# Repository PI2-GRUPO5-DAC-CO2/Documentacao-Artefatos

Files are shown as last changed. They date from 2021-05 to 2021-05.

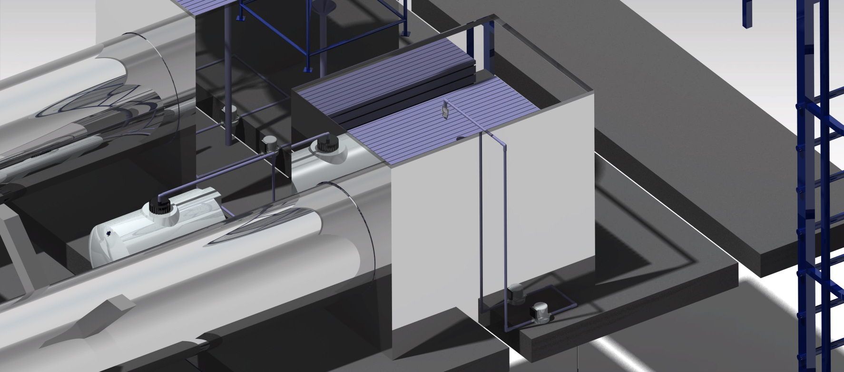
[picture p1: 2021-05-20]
Engenharias/Estruturas/PC3/Prints FINAIS/RENDER 4.jpg

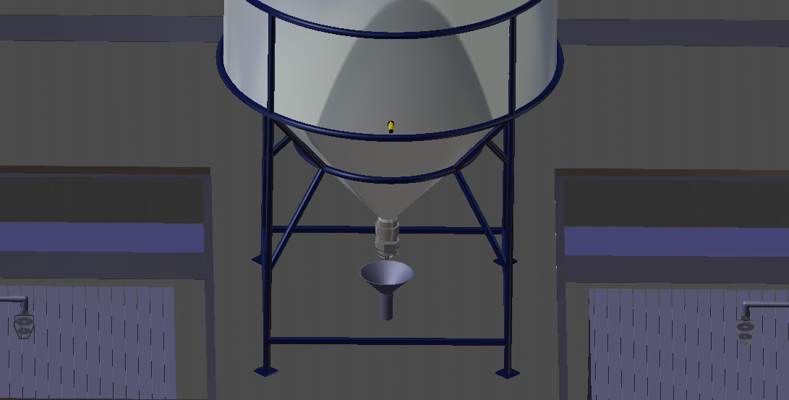
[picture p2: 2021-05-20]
Engenharias/Eletrônica/Integração/Integração - estrutura/Prints da Integração/Reservatorio Hidroxido.jpg

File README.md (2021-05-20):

# Projeto CATARCO

## Os links das apresentações  se encontram a seguir.

Ponto de controle 1: https://youtu.be/nJo-AYe7SZ8      

Ponto de controle 2: https://youtu.be/koXnGq-lNKc             

Ponto de controte 3: https://youtu.be/X2KLboLLJJk               

Feira de inovação de Tecnologia - FIT: https://youtu.be/X2KLboLLJJk

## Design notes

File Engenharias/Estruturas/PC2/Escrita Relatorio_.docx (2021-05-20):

Estrutura Externa

1 Materiais e justificativa

1.2Reservatórios

1- NA2CO3-- FEITO

2- CA(OH)2 -- Feito

3-NAOH --FEITO

4- CaCO3-- FEITO

1.6-Tubulações

Simulação estrutural

-NAOH---

-CAO3--

CA(OH2)- Geometria

Para a solução do formato do reservatório,foi levado em consideração o estado físico do CA(OH 2), por ser sólido em temperatura ambiente em forma de Pó fino, para transportá-lo para outros processos necessitaria a disposição de uma bomba especial. Por esse motivo, o reservatório foi instalado na parte superior da estrutura, usando a gravidade para o seu transporte. A geometria que mais se encaixa na solução é a cônica, onde não tem necessidade de intervenção para para descer. O volume calculado para o armazenamento do CACO3 é cerca de 756L, foi dimensionado um reservatório de capacidade 800L, para encontrar soluções prontas na indústria.

NA2CO3- - Geometria

Para o armazenamento da substância NA2CO3, foi calculada que o volume necessário é 192L, no entanto a disposição do tanque será na parte de cima da estrutura, onde não podemos ter um reservatório de alto pois impedia instalação por causa dos ventiladores, foi usado a solução de reservatório horizontal de capacidade de 230 Litros, onde os suportes são feito do mesmo material do reservatório, como mostrado na FigX

CACO3-DEFINIÇÃO GEOMETRIA

A Definição de geometria do reservatório, levou em consideração as soluções usadas comercialmente para armazenamento de substâncias químicas, pensando em ser em ter o maior volume com a menor área ocupada, foi escolhida novamente a forma Cilíndrica e fundo cônico ccmo na Fig X

CACO3-DEFINIÇÃO Suporte

O suporte foi dimensionado com o mesmo perfil tubular do NaOH, com 1 Polegada Com 1,5 mm de diâmetro interno, sendo todo o peso sustentado pelo tubo de raio menor junto com os suportes laterais, e os tubos superiores evitando o deslocamento do reservatório, deixando a estrutura mais estática possível .

CACO3-DEFINIÇÃO Material

O material utilizado nos suportes foi padrão para todos os os reservatórios, o aço 316,por possuir ótima propriedades mecânicas e possui uma ótima resistência à corrosão em comparação a outros tipos de aço.

CACO3-DEFINIÇÃO Qualidade da malha

Para a geração da malha, foi levada em consideração uma maior geração de elementos onde a estrutura vai ser sofrer mais esforços, nos suporte circulares,e nas pernas de apoio, foi utilizado uma malha de 5mm, onde encontramos uma qualidade satisfatória para realizar a simulação , Fig podemos ver que mesmo não.

CACO3-DEFINIÇÃO Condições de Contorno

São similares aos reservatório de NaOH e CaOH2, por se tratar de um sistema estático de armazenamento, únicos esforços são a força peso feita massa de Cao3 no sistema, com o valor máximo de 330 KG com o peso do suporte, foi considerado uma carga de 3300N como na Fig X

CACO3-DEFINIÇÃO Análise estática e resultados

A partir das condições de contorno aplicadas à geometria, a análise estática do suporte foi feita sob o modelo de flexão, o critério adotado em outros tópicos é de tensão de escoamento do material Tab X. Com a análise visa o resultados tensão de von Mises e o valor de deformação total do material que seguem descritos nas Fig. X e X

Os resultados obtido mostram que a estrutura atende muito bem a solicitações exigidas para o que foi projetada, com o deslocamento máximo de 0.061 mm e tensão de 20.417 MPA, sendo menor que a tensão de escoamento do material de 250 MPA,

NAOH-DEFINIÇÃO GEOMETRIA

Para o reservatório de naoh foi calculado o volume de 121 L para o sistema pode fazer um ciclo processamento do Co2, e levando em consideração que a norma NBR-15762 pede um volume de sgurança 30 \%, foi dimensionado um volume total de 160 L, utilizando a forma cilíndrica que o padrão reservatórios de PEAD.

NAOH-Definição suporte e geometria

Para a estrutura de suporte do reservatório, foi escolhido o modelo já utilizado comumente utilizado pela indústria, suporte tubular de 1 Polegada e 1,5 mm de diâmetro. O suporte como visto na fig X, concentra todo peso no anel tubular de menor raio, junto com suportes laterais, o mesmo foi projetado para receber somente carga do peso do reservatório mais fator de segurança.

Definição do material}

O material utilizado na estrutura foi o Aço 316, por causa das suas ótima propriedades químicas e mecânicas já comentadas no tópicos X

Qualidade da malha}

Para geração da malha, foi considerado onde a estrutura tem mais esforços, o suporte anelar do meio sustenta toda a estrutura, juntos com suportes laterais, então a malha foi maior refinada na área a ter encontrar um valor de qualidade aceitável para validação da solução, como mostra a FIG X

Condições de contorno}

Por se tratar de um reservatório estático onde não temos nenhuma força além da massa armazenada, foi utilizado a carga de 2700 N sobre as faces do suporte circular para validar o uso com seu volume máximo de 160 L , aproximadamente 258 KG de Naoh .

Análise estática e resultados}

Analisando o resultado dos esforços da gerados na geometria , a análise estática da estrutura foi feita considerando o modelo de flexão, a deformação máxima do suporte foi de 0.59 mm no anel de suporte como mostrado na Fig X, a tensão de von Mises máxima calculada de 110,13 MPA, mostrado na Fig X, sendo bem menor que 250 MPA de tensão de escoamento do material. Dessa forma temos 2.27 de fator de segurança

1- NA2CO3

- Para armazenar a solução de NA2CO3, figura X não se encontra dificuldade para a seleção de material para armazenar , já que a solução não é corrosiva e não reage facilmente com qualquer substância conforme a FISPQ e conforme a ABNT NBR 14725-2:2019 essa mistura não se encaixa em produto não corrosivo, ou seja não há exigências específicas da legislação para armazenamento e transporte , somente o cuidado para manter na temperatura adequada, e em ambiente fechado.
- Como não temos limitação de material a ser armazenado, vamos utilizar uma solução bem conhecida da indústria, o Polietileno,. Material leve e de natureza não polar, ele possui alta estabilidade agentes químicos e outros meios, sendo resistentes a soluções aquosas de sais, ácidos inorgânicos e álcalis(FISPQ). Até 74 graus, os PE são estáveis a muitos solventes. Como vamos trabalhar com NaoH em algumas partes do processo do CARTAGO, é importante assegurar que, caso o reservatório de carbonato de sódio tenha contato com a solução, o mesmo não seja afetado quimicamente.
- o PE tem propriedades mecânicas e térmicas que satisfazem os requisitos definidos no PC1, como mostra a Tabela X

| Normas | PEAD
Tensão de escoamento (Mpa) | D-637 | 26
Temperatura mínima e máxima em uso contínuo | | - 40 / + 90°C
Temperatura de Deflexão Térmica ( Celsus) | D-648 | 74
Resistência a Bases fortes | ASTM D543 | Resistente
Alongamento até a ruptura (%) | DIN 53452 / ASTM D638 / ISO R 527 | 500%
Tensão de escoamento à tração (MPA) | DIN 53455 / ASTM D638 / ISO R 527 | 29 MPa

Tabela: Propriedades mecânica e Térmicas PP

Referência :

FISPQ

http://csmpq.com.br/wp-content/uploads/2017/11/FISPQ-11-Carbonato-de-S%C3%B3dio-07_2015.pdf

1- CA(OH)2

A substância CA(OH)2, também conhecida como Cal hidratada, é um produto químico muito utilizado na indústria de cimentos, de tratamento de água e na indústria civil na composição de tintas, argamassas e gessos. (FIGUEROA). Sólido em temperatura ambiente, é armazenado em forma de PÓ conforme a ABNT NBR 10790- 2016, é classificado como tóxico pela norma ABNT NBR 14725-4, no entanto não é classificado como perigoso e as normas não especificam material para armazenamento, somente cuidado de movimentação, pois é tóxico e precisa de EPIs específicos para uso.

Para a definição dos materiais do reservatório, Imagem X, levamos em conta, a absorção do material a água, já que a cal reage água de forma exotérmica ,peso específico ,resistência química para o NaOH, capacidade de armazenamento de substâncias sólidas e facilidade de soluções prontas na indústria. A tabela X de matriz de decisão foi feita para melhor visualização dos pesos.O PEAD foi o material escolhido por ter a maior nota, e por isso se adequa a nossa solução.

Matriz de decisão do material
Critérios | Peso | PEAD | Aço Inox 316 | Fibra de Vidro
Massa específica | 7 | 8 | 6 | 8
Preço | 8 | 8 | 5 | 6
Resistência mecânica | 6 | 8 | 9 | 8
Resistência à Corrosão | 9 | 9 | 9 | 9
Resultado | | 186 | 154 | 170

\begin{table}[]

\begin{tabular}{|c|c|c|c|c|}

\hline

\multicolumn{5}{|c|}{Matriz de decisão do material} \\ \hline

Critérios & Peso & PEAD & Aço Inox 316 & Fibra de Vidro \\ \hline

Massa específica & 7 & 8 & 6 & 8 \\ \hline

Preço & 8 & 8 & 5 & 6 \\ \hline

Resistência mecânica & 6 & 8 & 9 & 8 \\ \hline

Resistência à Corrosão & 9 & 9 & 9 & 9 \\ \hline

Resultado & \multicolumn{1}{l|}{} & 186 & 154 & 170 \\ \hline

\end{tabular}

\end{table}

Referência:

FIGUEROA, Oscar O. Loli; NEPTUNE, André M. Louis. Influência da aplicação parcelada do Ca(OH)2 e do fósforo na produção de matéria seca do sorgo (Sorghum bicolor L. Moench) e nas principais formas de fósforo do solo. An. Esc. Super. Agric. Luiz de Queiroz, Piracicaba , v. 44, n. 2, p. 959-999, 1987 . Available from <http://www.scielo.br/scielo.php?script=sci_arttext&pid=S0071-12761987000200005&lng=en&nrm=iso>. access on 11 Apr. 2021. http://dx.doi.org/10.1590/S0071-12761987000200005.

ABNT NBR 10790- 2016

https://www.abntcatalogo.com.br/norma.aspx?ID=364269

ABNT NBR 14725-4

https://www.abntcatalogo.com.br/norma.aspx?ID=325473

1 . Reservatório de NAOH

- Para o reservatório de NAOH na Figura X foi encontrada uma série de restrições físicas e químicas e de normas impostas pela ABNT, ele é classificado pela norma ABNT 14725-4 como material altamente corrosivo e tóxico. A soda cáustica aquosa é uma substância muito corrosiva a materiais metálicos , como Alumínio, zinco, estanho e suas ligas, conforme a FISPQ do material. Recomenda-se a usar no reservatório materiais não reativos a NAOH, como aço carbono e aço inoxidável e certos compostos termoplásticos, como PP (Polipropileno) e PVC. Para a escolha do material levamos em consideração a temperatura de trabalho e de armazenamento do NAOH, pois em alta temperatura ele ataca o aço em altas temperaturas de trabalho. Outro fator importante a destacar é o biológico, a mistura ataca qualquer substância orgânica, e por isso é prejudicial ao homem, por isso no manuseio de substâncias deve levar em consideração a ABNT 16310. Como requisito de projeto, definido no Ponto de controle 1, o NAOh vai ser armazenado a uma temperatura máxima de 45 graus.
- Levando em consideração a FISPQ E ABNT 16310, os reservatórios que forem utilizar aço carbono ou aço inoxidável, é recomendado a não passar de 60 Graus, acima disso a aço precisa de tratamento diferente e adicionamento de substâncias, o que deixa o preço maior. Para o uso de termoplásticos, como a temperatura de uso recomendado pelas fabricantes é de 65 graus, variando com o nível de concentração.
- Levando em conta as informações e requisitos do sistema, a matriz de decisão X, traz informações dos principais materiais para essa aplicação, utilizando pesos que podem ser traduzidos em nível de importância para o projeto.Para a definição dos pesos, foi levado em consideração as necessidades do produto, facilidade de aquisição do material , modos e facilidades de fabricação e o custo de aquisição do material e do produto final. Estes pontos são destacados devido à natureza do projeto: um produto muito caro prejudica a instalação de diversas estações ao longo do terreno e o custo de material,a disponibilidade no mercado e as possibilidades de fabricação são fundamentais para o custo do produto.
- Conforme o resultado da matriz de decisão X, o PEAD é a melhor escolha para o projeto Cartaco, face aos materiais analisados. O Polipropeno é um material de fácil aquisição no mercado em diversas especificações,fácil logística, médio/baixo custo e pode ser encontrado com uma grande facilidade. Além disso, existem estudos técnicos, o que implica no maior conhecimento de suas propriedades e respostas devido ao seu manuseio e operação.
- \begin{table}[]
- \begin{tabular}{|c|c|c|c|c|c|}
- \hline
- \multicolumn{6}{|c|}{\textbf{Matriz de decisão do material}} \\ \hline
- Critérios & Peso & Polipropileno(PEAD) & Aço Inox 316 & Aço Duplex & Fibra de Vidro \\ \hline
- Massa específica & 4 & 8 & 6 & 8 & 8 \\ \hline
- Preço & 8 & 8 & 5 & 4 & 6 \\ \hline
- Resistência mecânica & 6 & 8 & 9 & 10 & 8 \\ \hline
- Resistência à Corrosão & 10 & 9 & 9 & 9 & 9 \\ \hline
- Resultado & \multicolumn{1}{l|}{} & \textbf{163} & 137 & 143 & 147 \\ \hline
- \end{tabular}
- \end{table}

Matriz de decisão do material
Critérios | Peso | Polipropileno(PEAD) | Aço Inox 316 | Aço Duplex | Fibra de Vidro
Massa específica | 4 | 8 | 6 | 8 | 8
Preço | 8 | 8 | 5 | 4 | 6
Resistência mecânica | 6 | 8 | 9 | 10 | 8
Resistência à Corrosão | 10 | 9 | 9 | 9 | 9
Resultado | | 163 | 137 | 143 | 147

PROPRIEDADES FÍSICAS | NORMAS | VALORES
Peso específico | DIN 53479 / ASTM D792 / ISO 1183 | 0,95 g/cm³
Temperatura mínima e máxima em uso contínuo | | - 40 / + 90°C
Tensão de escoamento à tração | DIN 53455 / ASTM D638 / ISO R 527 | 29 MPa
Resistência à bases fortes | ASTM D543 | resistente

Tabela PEAD

\begin{table}[]

\begin{tabular}{llllll}

\cline{1-3}

\multicolumn{1}{|l|}{PROPRIEDADES FÍSICAS} & \multicolumn{1}{l|}{NORMAS} & \multicolumn{1}{l|}{VALORES} & & & \\ \cline{1-3}

\multicolumn{1}{|l|}{Peso específico} & \multicolumn{1}{l|}{DIN 53479 / ASTM D792 / ISO 1183} & \multicolumn{1}{l|}{0,95 g/cm³} & & & \\ \cline{1-3}

\multicolumn{1}{|l|}{Temperatura mínima e máxima em uso contínuo} & \multicolumn{1}{l|}{} & \multicolumn{1}{l|}{- 40 / + 90°C} & & & \\ \cline{1-3}

\multicolumn{1}{|l|}{Tensão de escoamento à tração} & \multicolumn{1}{l|}{DIN 53455 / ASTM D638 / ISO R 527} & \multicolumn{1}{l|}{29 MPa} & & & \\ \cline{1-3}

\multicolumn{1}{|l|}{Resistência à bases fortes} & \multicolumn{1}{l|}{ASTM D543} & \multicolumn{1}{l|}{resistente} & & & \\ \cline{1-3}

& & & & & \\

& & & & & \\

& & & & &

\end{tabular}

\end{table}

Referências :

FISQ

https://www.santos.sp.gov.br/static/files_www/conteudo/DadosAbertos/FISPQ%20Soda%20c%C3%A1ustica.pdf

ABNT

https://www.normas.com.br/visualizar/abnt-nbr-nm/34421/abnt-nbr16310-expedicao-transporte-rodoviario-e-recebimento-de-hidroxido-de-sodio-soda-caustica-em-solucao-a-g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

https://www.abntcatalogo.com.br/norma.aspx?ID=325473

1.3 Reservatório de CACO3

O carbonato de Cálcio, conforme a norma ABNT NBR 14725-2:2019, quanto a classificação, a solução é classificada como uma mistura na reativa e não corrosiva, a escolha do material não precisa ter os mesmo nível de rigidez que o reservatório de NAOH (Tópico) tem, pois a legislação não especifica materiais específicos para armazenamento. Levando isso em consideração, podemos simplificar a busca por materiais leves, baratos e de fácil manutenção e que seja inerte a solução de soda cáustica, caso tenha contato.

Nesse perfil temos o Polietileno PP, mesmo material utilizado no reservatório de Carbonato de sódio, resistente ao NaOh e tem ótima propriedades mecânicas, vista na tabela X INCOMPLAST.

O PP, é um material de fácil aquisição no mercado em diversas especificações, fácil logística e baixo custo, e para o reservatório de CaCo3 precisamos de um tanque como na figura X de capacidade menor que nos outros processos do Cartago.

| Normas | PEAD
Tensão de escoamento (Mpa) | D-637 | 26
Temperatura mínima e máxima em uso contínuo | | - 40 / + 90°C
Temperatura de Deflexão Térmica ( Celsus) | D-648 | 74
Resistência a Bases fortes | ASTM D543 | Resistente
Alongamento até a ruptura (%) | DIN 53452 / ASTM D638 / ISO R 527 | 500%
Tensão de escoamento à tração (MPA) | DIN 53455 / ASTM D638 / ISO R 527 | 29 MPa

Tabela: Propriedades mecânica e Térmicas PP

\begin{table}[]

\begin{tabular}{llllll}

\cline{1-3}

\multicolumn{1}{|l|}{} & \multicolumn{1}{l|}{Normas} & \multicolumn{1}{l|}{PEAD} & & & \\ \cline{1-3}

\multicolumn{1}{|l|}{Tensão de escoamento (Mpa)} & \multicolumn{1}{l|}{D-637} & \multicolumn{1}{l|}{26} & & & \\ \cline{1-3}

\multicolumn{1}{|l|}{Temperatura mínima e máxima em uso contínuo} & \multicolumn{1}{l|}{} & \multicolumn{1}{l|}{- 40 / + 90°C} & & & \\ \cline{1-3}

\multicolumn{1}{|l|}{Temperatura de Deflexão Térmica ( Celsus)} & \multicolumn{1}{l|}{D-648} & \multicolumn{1}{l|}{74} & & & \\ \cline{1-3}

\multicolumn{1}{|l|}{Resistência a Bases fortes} & \multicolumn{1}{l|}{ASTM D543} & \multicolumn{1}{l|}{Resistente} & & & \\ \cline{1-3}

\multicolumn{1}{|l|}{Alongamento até a ruptura (\%)} & \multicolumn{1}{l|}{DIN 53452 / ASTM D638 / ISO R 527} & \multicolumn{1}{l|}{500\%} & & & \\ \cline{1-3}

\multicolumn{1}{|l|}{Tensão de escoamento à tração (MPA)} & \multicolumn{1}{l|}{DIN 53455 / ASTM D638 / ISO R 527} & \multicolumn{1}{l|}{29 MPa} & & & \\ \cline{1-3}

& & & & &

\end{tabular}

\end{table}

Referências

INCOMPLAST. POLIPROPILENO (PP). 2019. Disponível em: <https://incomplast.

com.br/polipropilenopp/>. Acesso em: 1 abr. 2021.

2 -Tubulações

Para a escolha de materiais das tubulações, temos que levar em consideração que algumas partes do projeto vão ter contato com NaOH, outras não.

Para padronizar o projeto foi escolhido escolher somente um tipo de material para as tubulações.

Temos que escolher um material de uma longa vida útil, resistente ao trabalho com temperatura acima de 45 graus, e ação do NAOH, baixo custo, fácil manutenção e usinagem .

Foi elaborada uma matriz de decisão X para escolha do material dos tubos, a tabela traz informações dos principais materiais que é utilizado para essa aplicação e o resultado mais adequado para o projeto, utilizando pesos que podem ser traduzidos em nível de prioridade.

Com o CPVC (Cloriploreto de Vinila Clorado) como resultado da matriz de decisão, podemos dizer que é a melhor escolha para o projeto, por ser um material de fácil instalação e manutenção, boa resistência mecânica ,confiável para transportes de produtos químicos a altas temperaturas, até 90 graus. Além de ser um produto de fácil aquisição no mercado.

Matriz de decisão do material
Critérios | Peso | Polietileno | PVC | CPVC | Aço Inox
Incrustação/Perda de pressão | 7 | 8 | 7 | 8 | 7
Preço | 8 | 7 | 9 | 8 | 5
Resistência mecânica/Impactos/Pressão | 6 | 7 | 6 | 7 | 9
Resistência à Corrosão/Temperatura | 9 | 8 | 7 | 8 | 9
Massa específica | 7 | 9 | 8 | 8 | 5
Resultado | | 234 | 229 | 235 | 196

\begin{table}[]

\begin{tabular}{|c|c|c|c|c|c|}

\hline

\multicolumn{6}{|c|}{Matriz de decisão do material} \\ \hline

Critérios & Peso & Polietileno & PVC & CPVC & Aço Inox \\ \hline

Incrustação/Perda de pressão & 7 & 8 & 7 & 8 & 7 \\ \hline

Preço & 8 & 7 & 9 & 8 & 5 \\ \hline

Resistência mecânica/Impactos/Pressão & 6 & 7 & 6 & 7 & 9 \\ \hline

Resistência à Corrosão/Temperatura & 9 & 8 & 7 & 8 & 9 \\ \hline

Massa específica & 7 & 9 & 8 & 8 & 5 \\ \hline

Resultado & \multicolumn{1}{l|}{} & 234 & 229 & \textbf{235} & 196 \\ \hline

\end{tabular}

\end{table}

\begin{table}[]

\begin{tabular}{|l|l|l|}

\hline

PROPRIEDADES FÍSICAS & NORMAS & VALORES \\ \hline

Peso específico & DIN 53479 / ASTM D792 / ISO 1183 & 0,95 g/cm³ \\ \hline

Temperatura mínima e máxima em uso contínuo & & - 40 / + 90°C \\ \hline

Tensão de escoamento à tração & DIN 53455 / ASTM D638 / ISO R 527 & 29 MPa \\ \hline

Resistência à bases fortes & ASTM D543 & resistente \\ \hline

\end{tabular}

\end{table}

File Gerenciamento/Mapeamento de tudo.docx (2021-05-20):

Contator:

- Exaustor
  - Pás
  - Motor
  - Sensores
  - Atuador
    - automatizado
    - manual
  - Características
    - Vazão
    - potência
    - Dimensões …
- Estrutura de sustentação
- Quantidade
- Tempo da etapa
- Gasto energético
- Valor Total
- Simulações
- Filtro
  - Estrutura
    - material
    - Formato
      - Circular ou quadrado
      - colméia ou placas verticais por exemplo
    - Espessura
  - Sistema de recirculação do NaOH
    - bomba
    - tubulação
    - calha intermediária
    - atuadores
  - Quantidade
  - Sensores
  - Atuador
    - automatizado
    - manual
- Estrutura de sustentação
- Tempo da etapa
- Gasto energético
- Valor Total
- Simulações

Conexão 1 [Contator -> Reservatório 1]

- Tubulação
  - espessura da parede
  - material
  - Válvulas
  - Atuadores
    - manuais
    - automatizados
  - Sensores
  - Estrutura de sustentação
  - Tempo da etapa
  - Gasto energético
  - Valor Total
  - Simulações
- Bomba
  - tipo
  - sensores
  - atuadores
    - manuais
    - automatizados
- Estrutura de sustentação
- Tempo da etapa
- Gasto energético
- Valor Total
- Simulações

Reservatório 1 (NaCO3)

- Sensores
- atuadores
  - manuais
  - automatizados
- válvulas
- características
  - formato
  - dimensões
  - espessura da parede
  - peso
- Estrutura de sustentação
- Tempo da etapa
- Gasto energético
- Valor Total
- Simulações

Conexão 2 [Reservatório 1 -> Reator]

- Tubulação
  - espessura da parede
  - material
  - Válvulas
  - Atuadores
    - manuais
    - automatizados
  - Sensores
  - Estrutura de sustentação
  - Tempo da etapa
  - Gasto energético
  - Valor Total
  - Simulações

Reservatório 2 [Ca(OH)2]

- Sensores
- atuadores
  - manuais
  - automatizados
- válvulas
- características
  - formato
  - dimensões
  - espessura da parede
  - peso
- Estrutura de sustentação
- Tempo da etapa
- Gasto energético
- Valor Total
- Simulações

Conexão 3 [Reservatório 2 -> Reator]

- Tubulação
  - espessura da parede
  - material
  - Válvulas
  - Atuadores
    - manuais
    - automatizados
  - Sensores
  - Estrutura de sustentação
  - Tempo da etapa
  - Gasto energético
  - Valor Total
  - Simulações

Reator:

- Motor
- Pás
- Válvulas
- sensores
- Atuadores
  - manuais
  - automatizados
- Característica
  - material
  - Dimensões
  - Volume
  - formato
  - espessura da parede
- Estrutura de sustentação
- Tempo da etapa
- Gasto energético
- Valor Total
- Simulações

Conexão 4 [Reator -> Centrífuga]

- Tubulação
  - espessura da parede
  - material
  - Válvulas
  - Atuadores
    - manuais
    - automatizados
  - Sensores
  - Estrutura de sustentação
  - Tempo da etapa
  - Gasto energético
  - Valor Total
  - Simulações
- Bomba
  - tipo
  - sensores
  - atuadores
    - manuais
    - automatizados
- Estrutura de sustentação
- Tempo da etapa
- Gasto energético
- Valor Total
- Simulações

Centrífuga

- Válvulas
- tipo
- sensores
- atuadores
  - manuais
  - automatizados
- Estrutura de sustentação
- Tempo da etapa
- Gasto energético
- Valor Total
- Simulações

Conexão 5 [Centrífuga -> Reservatório 3]

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

Reservatório 3 [NaOH]

- Sensores
- atuadores
  - manuais
  - automatizados
- válvulas
- características
  - formato
  - dimensões
  - espessura da parede
  - peso
- Estrutura de sustentação
- Tempo da etapa
- Gasto energético
- Valor Total
- Simulações
- Estrutura de suporte

Conexão 6 [Reservatório 3 -> Contator]

- Tubulação
  - espessura da parede
  - material
  - Válvulas
  - Atuadores
    - manuais
    - automatizados
  - Sensores
  - Estrutura de sustentação
  - Tempo da etapa
  - Gasto energético
  - Valor Total
  - Simulações
- Bomba
  - tipo
  - sensores
  - atuadores
    - manuais
    - automatizados
- Estrutura de sustentação
- Tempo da etapa
- Gasto energético
- Valor Total
- Simulações

Conexão 7 [Centrífuga -> Reservatório 4]

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

Reservatório 4 [CaCO3]

- Sensores
- atuadores
  - manuais
  - automatizados
- válvulas
- características
  - formato
  - dimensões
  - espessura da parede
  - peso
- Estrutura de sustentação
- Tempo da etapa
- Gasto energético
- Valor Total
- Simulações
- Estrutura de suporte

Sala de operação

- Características
  - dimensões
- Sistema de contenção
- Disposição dos componentes
- Estrutura Externa
- Gasto energético
- Valor Total
- Simulações
  - Estrutura externa
- Central de Comando
  - Monitor
  - Painel

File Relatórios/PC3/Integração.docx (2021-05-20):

Integração

- Sistema de comunicação
  - João
  - (alguém de soft)
- Funções de software
- Relação das necessidades de eletrônica com as escolhas de energia
  - Marcelo
- Bombas, tubulações (Sugestão de nome para o tópico: Sistema de circulação para fluidos e sólidos)

- Marcelo

- Explicar porque tal sensor e atuador está localizado em tal lugar (Sugestão de nome para o tópico: Instalação de sistema eletrônico)
  - (Sugestão de nome para o tópico: Sistema de circulação para fluidos e sólidos)

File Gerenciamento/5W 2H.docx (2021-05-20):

Descrição do projeto

Para descrever o projeto CATARCO, foi utilizado a ferramenta 5W2H, termo que corresponde às iniciais (em inglês) de sete questionamentos capazes de guiar e sanar as principais dúvidas que podem surgir ao longo do projeto. O modelo é apresentado abaixo.

- What (o que será feito?)

Será criado um sistema semi-automático de captura de gás carbônico do ar para produção de carbonato de cálcio que permite acompanhamento remoto.

- Why (por que será feito?)

Para minimizar os danos causados pela emissão de gás carbônico na atmosfera, produzindo ainda o carbonato de cálcio.

- Where (onde será feito?)

Universidade de Brasília

- When (quando será feito?)

De fevereiro a maio de 2021

- Who (por quem será feito?)

Alunos de engenharia da Faculdade UnB Gama. A lista dos integrantes do projeto bem como suas funções podem ser observadas na tabela X.

- How (como será feito?)

O projeto utilizará o conhecimento que envolve as cinco engenharias presentes no campus Gama da Universidade de Brasília e será realizado de forma remota. Devido a isto, será realizada apenas a documentação técnica e demais artefatos que corroboram para a viabilidade do projeto.

- How much(quanto vai custar?)

O projeto possui investimento estimado de R$ XX,XX. A tabela X1 apresenta o detalhamento do orçamento estimado.

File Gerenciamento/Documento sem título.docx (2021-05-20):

Código:

- Funções do cálculo de eficiência
- Funções de que consomem dados da rede IoT
- Funções de controle da estação
- Funções de comunicação Back-Front

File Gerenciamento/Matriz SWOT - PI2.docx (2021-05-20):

ANÁLISE SWOT

| POSITIVO | NEGATIVO

I

N

T

E

R

N

A

Forças

- Por se tratar de um protótipo, o projeto permite estudar a viabilidade sem a necessidade de grandes recursos, reduzindo riscos e custos
- Equipe multidisciplinar
- Projeto pode ser enquadrado como empreendedorismo sustentável
- Além de contribuir para preservar as condições de existência da humanidade na terra, o projeto gera um produto que pode ser comercializado
- O carbonato de cálcio produzido possui alto grau de pureza
- Sistema de controle inteligente que auxilia o monitoramento
- Projeto pode ser dimensionado para aplicações maiores

Fraquezas

- Pouco conhecimento na área de química, que se mostra fundamental para o projeto
- Alto valor necessário para a implementação do projeto físico
- Por se tratar de uma escala reduzida (protótipo), o projeto pode não despertar o interesse de investidores
- Alto gasto energético limita sua aplicação a pólos industriais ou locais com grande disponibilidade energética
- Necessidade de materiais que não reajam com NaOH limita a escolha de materiais para estrutura e componentes eletrônicos
- Por conter soluções químicas, o projeto precisa atender várias normas de segurança para garantir sua aplicabilidade e evitar acidentes

EXTERNA | Oportunidades - Conscientização das pessoas para questões ecológicas - Existência de regulamentações e tratados, como Protocolo de Kyoto, para diminuição da emissão de CO2 pelas indústrias possibilita o mercado de carbono - Fato de ser um projeto que visa a sustentabilidade pode despertar interesse de empresas que se preocupam com essa questão - Disponibilidade de auxílio de professores para questões técnicas - Crescente o número de pesquisas de tecnologias como Blockchain e IoT que podem ser aplicadas ao negócio | Ameaças - Pouca disponibilidade de componentes que sejam resistentes às soluções - Competitividade com outras abordagens de redução de CO2 na atmosfera - Grandes períodos chuvosos podem dificultar a captura de carbono - Prazos curtos para finalização do projeto - Valor de produtos importados variam com relação à moeda

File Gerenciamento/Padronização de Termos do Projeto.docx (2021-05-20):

Padronização de Termos do Projeto

Em Relação ao Sistema

Sistema de absorção:

- Definição: Dois módulos, composto por um exaustor e um filtro, cada.
- Nome alternativo: Componente 1 (C1)
- Composto: Módulo 1 do Sistema de absorção de Ar ou Componente 1.1 (C1.1)

Módulo 2 do Sistema de absorção de Ar ou Componente 1.2 (C1.2)

Exaustor:

- Definição: “ventilador” que puxa o ar

Filtro de captura:

- Definição: Onde há a captura do CO2
- Nome alternativo: Filtro

Reator Químico

- Definição: Onde há a reação química do Ca(OH) + Na2CO3 -> CaCO3 + NaOH
- Nome alternativo: Componente 2 (C2) ou Reator

Separador centrífugo

- Definição: Onde há a separação do CaCO3 + NaOH
- Nome alternativo: Componente 3 (C3)

Reservatório de Na2CO3

- Definição: Armazena o produto gerado (Na2CO3) na captura do CO2 que ocorre no Filtro de Captura do Contator
- Nome alternativo: Reservatório 1(R1)

Reservatório de Carbonato de Sódio

Reservatório de Ca(OH)2

- Definição: Armazena o Ca(OH)2 usado na reação química do reator
- Nome alternativo: Reservatório 2(R2)

Reservatório de Hidróxido de Cálcio

Reservatório de NaOH

- Definição: Armazena o NaOH usado na captura do CO2
- Nome alternativo: Reservatório 3(R3)

Reservatório de Hidróxido de Sódio

Reservatório de Soda Cáustica

Reservatório de CaCO3

- Definição: Armazena o CaCO3, produto de todo o processo
- Nome alternativo: Reservatório 4(R4)

Reservatório de Carbonato de Cálcio

Conexão 1

- Definição: Ligação entre o Contator e o Reservatório 1
- Composto: Tubulações e Bombas 1 e Bomba 2

Bomba 1

- Definição: bomba que realimenta o filtro do Módulo 1 do Contator
- Nome alternativo: Bomba de Circulação do Módulo 1

Bomba 2

- Definição: bomba que realimenta o filtro do Módulo 2 do Contator
- Nome alternativo: Bomba de Circulação do Módulo 2

Bomba 3 e 4

- Definição: bombas que enviam a solução das calhas para o Reservatório 1
- Nome alternativo: Bomba de direcionamento de fluido (? Aceita novas sugestões)

Conexão 2

- Definição: Ligação entre o Reservatório 1 e o Reator

Conexão 3

- Definição: Ligação entre o Reservatório 2 e o Reator

Conexão 4 [Reator -> Centrífuga]

Conexão 5 [Centrífuga -> Reservatório 3]

Conexão 6 [Reservatório 3 -> Contator]

Conexão 7 [Centrífuga -> Reservatório 4]

Eletroválvula 1

- Definição: Mecanismo eletromecânico capaz de controlar o fluxo de líquido nas tubulações
- local: Conexão 6
- Bitola: 1”

Eletroválvula 2

- Definição: Mecanismo eletromecânico capaz de controlar o fluxo de líquido nas tubulações
- local: Conexão 2
- Bitola: 1”

Eletroválvula 3

- Definição: Mecanismo eletromecânico capaz de controlar o fluxo de líquido nas tubulações
- local: Conexão 4
- Bitola: 1 1/2”

Eletroválvula 4

- Definição: Mecanismo eletromecânico capaz de controlar o fluxo de líquido nas tubulações
- local: Conexão 5
- Bitola: 1”

Dispenser

- Definição: Mecanismo eletromecânico que controla o fluxo do reagente sólido
- Local: Conexão 3

Bomba de Realimentação do sistema

- Definição: Bomba com objetivo de levar o fluido recuperado de NaOH, do reservatório, até os módulos 1 e 2 do sistema de absorção de CO2
- Local: Próximo ao reservatório de NAOH
- nome alternativo: bomba 6

Bomba para produtos do reator

- Definição: Bomba com capacidade para levar o fluido com sólidos em suspensão (CaCO3) para o decantador centrífugo.
- Local: Após o reator.
- nome alternativo: Bomba 5

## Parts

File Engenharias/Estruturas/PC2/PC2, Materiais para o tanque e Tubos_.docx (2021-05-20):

Dique de contenção

Dentro do projeto Cartago, há uma etapa de armazenamento do NAOH, classificado pela ABNT, como substâncias corrosivas ou perigosas, ele gera risco para o patrimônio físico, para o meio ambiente e saúde do funcionário. A Norma ABNT NBR 75505, prevê a instalação de diques de contenção para dar mais segurança e vazamento do líquido no ambiente.

Para dimensionar os diques e bacias de contenção, deve-se calcular o volume do tanque + 50% do seu volume total. O material usado no dique e seu revestimento é de suma importância, pois ele tem que ser impermeável e ser resistente à corrosão. Foi escolhido o Aço Inox 316, por ser utilizado na indústria química, farmacêutica e petróleo por causa de suas ótima resistência à corrosão , e suas características mecânicas para suportar o volume dimensionado quando houver necessidade.

Solução Estrutural ( Resumo )

- A solução estrutural deve ser baseada de acordo com as normas técnicas como NBR 15762. Caso o volume dos reservatórios seja maior que 1000 L é a norma técnica ABNT NBR 14725-2:201 que regula, para segurança do operador e do meio ambiente .
- Para a estrutua seguir com as norma de segurança, algumas modificações devem ser feitas, como por exemplo:
- O local deve ser ventilado, pois não pode haver névoa provocada pelos gases liberados do contato da água com a soda.
- Deve ser ter Chuveiro de emergência e Lava olhos no ambiente
- Deve ser o Dique de contenção caso haja ruptura do Naoh no ambiente, a exemplo a NBR 7505 para tanques grande de combustíveis– ser construídos diques de contenção para impedir qualquer derramamento ou gotejamento no meio ambiente.(Verificar obrigatoriedade deste item)
- A construção dos diques Devem ser construídos em alvenaria, com resistência à pressão hidrostática e dinâmica de um esvaziamento brusco do tanque, A área de construção deve corresponder ao volume somado dos tanques envolvidos, mais 10%, respeitando-se uma altura livre interna de aproximadamente 0,45 m, com previsão de esvaziamento por bomba de sucção. Não deve haver aberturas laterais com válvulas, e o revestimento interno deve resistir à ação química do líquido contido durante o período necessário até a remediação do respingo ou vazamento e a transferência para um vaso emergencial.

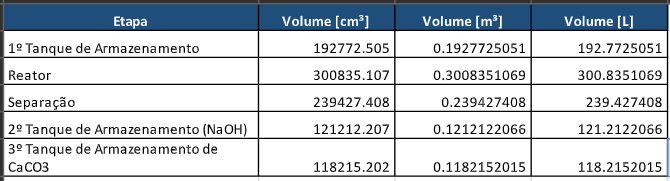
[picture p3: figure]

https://www.polybrasil.com.br/wp-content/uploads/2018/08/datasheet-ptfe-poli.pdf

Reservatório de carbonato de sódio e Água -- 192 L (OK) Concluído

- Para armazenar a solução de NA2CO3 não se encontra dificuldade para a seleção de material, já que a solução não é corrosiva e não reage facilmente com qualquer substância conforme a FISPQ (FICHA DE INFORMAÇÕES DE SEGURANÇA DE PRODUTOS QUÍMICOS) e conforme a ABNT NBR 14725-2:2019 essa mistura não se encaixa em produto não corrosivo, ou seja não há exigências específicas da legislação para armazenamento e transporte , somente o cuidado para manter na temperatura adequada, e em ambiente fechado.
- Como não temos limitação de material a ser armazenado, vamos utilizar uma solução bem conhecida da indústria, o Polietileno, especificamente o PEAD (Polietileno de Alta densidade). Material leve e de natureza não polar, ele possui alta estabilidade agentes químicos e outros meios, sendo resistentes a soluções aquosas de sais, ácidos inorgânicos e alcalis. Até 74 graus, os PEAD são estáveis a muitos solventes.
- Como vamos trabalhar com NaoH em algumas partes do processo do CARTAGO, é importante assegurar que, caso o reservatório de carbonato de sódio tenha contato com a solução, o mesmo não seja afetado quimicamente.
- O PEAD, tem propriedades mecânicas e térmicas que satisfazem os requisitos definidos no PC1, como mostra a Tabela abaixo
- A ASTM-D1998 regra para espessura de tanques de PEAD

Propriedades | Normas | PEAD
Tensão de escoamento (Mpa) | D-637 | 26
Temperatura mínima e máxima em uso contínuo | | - 40 / + 90°C
Temperatura de Deflexão Térmica ( Celsus) | D-648 | 74
Resistência a Bases fortes | ASTM D543 | Resistente
Alongamento até a ruptura (%) | DIN 53452 / ASTM D638 / ISO R 527 | 500%
Tensão de escoamento à tração (MPA) | DIN 53455 / ASTM D638 / ISO R 527 | 29 MPa

Tabela: Propriedades mecânica e Térmicas PEAD

Segue um exemplo de desenho Técnico para fazer o CAD

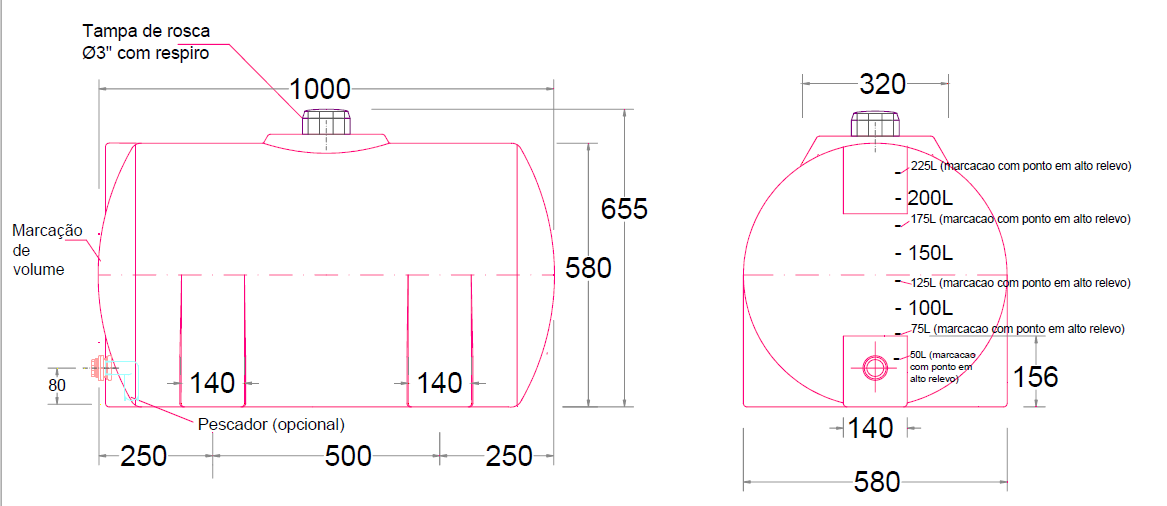
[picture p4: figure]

Referências:

https://incomplast.com.br/polietileno-pead/

COUTINHO, Fernanda M. B.; MELLO, Ivana L.; SANTA MARIA, Luiz C. de. Polietileno: principais tipos, propriedades e aplicações. Polímeros, São Carlos , v. 13, n. 1, p. 01-13, Jan. 2003 . Available from <http://www.scielo.br/scielo.php?script=sci_arttext&pid=S0104-14282003000100005&lng=en&nrm=iso>. access on 02 Apr. 2021. https://doi.org/10.1590/S0104-14282003000100005.

https://www.braskem.com.br/Portal/Principal/Arquivos/html/boletm_tecnico/Resistencia_quimica%20_PE.pdf

A ABNT NBR 14725-2:2019 equivale ao conjunto ABNT NBR 14725-2:2009 Versão corrigida:2010 e Emenda 1, de 13.06.2019.

https://www.hd.ind.br/PDF/H250.pdf

Reator Químico 3 - 300 L ( Verificar com Renato solução Escolhida)

- O Reator irá receber o fluido de solução Na2CO3 + H20. Dentro do reator terá uma solução de Ca(OH)2, a qual irá reagir com o fluido. O reator será comportado de uma uma placa giratória que estará em constante movimento, funcionando como um agitador. A solução para o material foi feita usando a matriz de decisão na tabela 1, mistura que ocorrerá é exotérmica e libera gases corrosivos, com isso o material tem que suporta uma temperatura de trabalho a entre 80 a 100 graus e as vibrações mecânica do reator e não pode reagir com a mistura .
- A temperatura de trabalho do reator precisa ser calculada, para podermos dimensionar e escolher o material.

Reservatório de carbonato de cálcio CACO3 -- Volume 118 L

- Para o carbonato de cálcio é mesma regra conforme a ABNT NBR 14725-2:2019 , a solução é classificada como uma mistura não reativa e não corrosiva, a escolha do material não precisa ter preocupação da regras NBR que o reservatório de NAOH tem, pois a legislação não especifica onde tem que ser armazenado, levando isso em conta podemos simplificar a busca por materiais leves, baratos e de fácil manutenção e que por algum motivo venha ter contato com a soda cáustica não venha reagir com respingos e ou vazamentos .
- Nesse perfil de material temos o Polietileno, mesmo material utilizado no reservatório de Carbonato de Sódio, resistente ao NaOH e tem ótimas propriedades mecânica e térmicas que se adequam ao uso, como segue na tabela(Colocar mesma tabela do Na2CO3)
- O PEAD, é um material de fácil aquisição no mercado em diversas especificações, fácil logística e baixo custo. Além disso existe uma extensa gama de estudos técnicos da PEAD, o que implica no maior conhecimento de suas propriedades e respostas devido ao seu manuseio e operação.
- Para a solução do Carbonato de Calcio, nao precisamos de um tanque capacidade um pouco inferior, valores mostrado abaixo

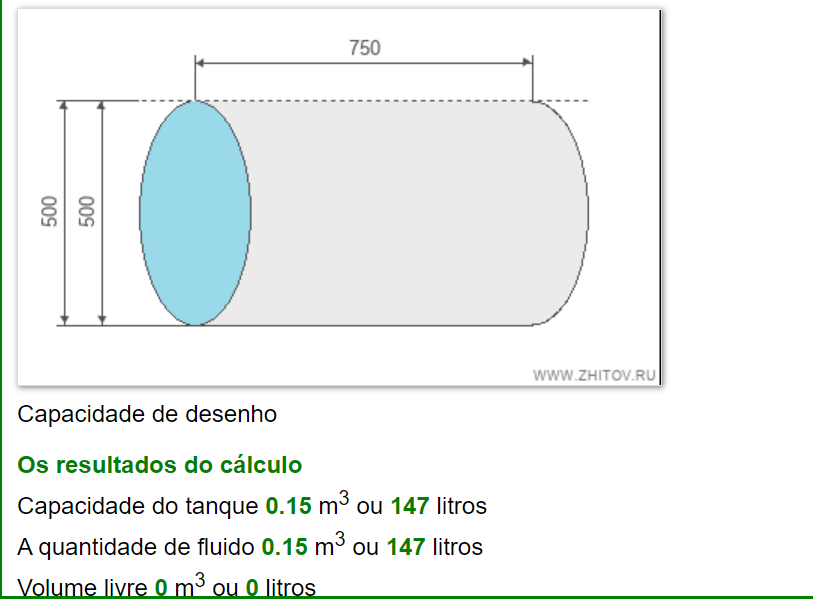
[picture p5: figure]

Reservatório de Hidróxido de cálcio\

Como se trata de uma substância sólida é tóxica para o ser humano, alguns cuidados precisam ser tomado na armazenagem, uso do EPi é obrigatório,

Para seleção de materiais

Reservatório de NAOH -- 121 L - Concluido

- Para o reservatório de NAOH encontramos uma série de restrições físicas e químicas e de normas impostas pela ABNT, por ser uma material altamente corrosivo e tóxico. A soda cáustica aquosa é uma substância muito corrosiva a materiais metálicos , como Alumínio, zinco, estanho e suas ligas, conforme a FISPQ do material. Recomenda-se a usar no reservatório materiais não reativos a NAOH , como aço carbono e aço inoxidável e certos compostos termoplásticos, como PP e PVC. Mas deve-se estar atento à temperatura de trabalho e de armazenamento do NAOH, pois em alta temperatura ele ataca o aço em altas temperaturas de trabalho. Outro fator importante a destacar é o biológico, a mistura ataca qualquer substância orgânica, e por isso é prejudicial ao homem, no projeto dos reservatórios deve-se ter medidas de segurança para o NaOh não vazar do reservatório. Para o projeto do reservatório foi definido uma temperatura de trabalho de 45 graus no PC1.
- Por recomendação da FISPQ, o reservatórios que foram utilizados aço carbono ou aço inoxidável não deve passar da temperatura de 60 graus, e para os reservatórios que foram utilizar algum tipo de plásticos. tal como o polipropileno, as empresas não recomendam trabalhar com temperatura acima de 65 graus
- Levando todas as recomendações do FISPQ e da ABNT, a tabela traz informações dos principais materiais para essa aplicação, e traz como resultado qual o mais adequado para o projeto, utilizando pesos que podem ser traduzidos como níveis de importância.
- Conforme resultado da matriz de decisão X, o PP é a melhor escolha para o projeto CARTAGO, face aos materiais analisados.Para a definição dos pesos, foi levado em consideração as necessidades do produto, facilidade de aquisição do material , modos e facilidades de fabricação e o custo de aquisição do material e do produto final. Estes pontos são destacados devido à natureza do projeto: um produto muito caro prejudica a instalação de diversas estações ao longo do terreno e o custo de material,a disponibilidade no mercado e as possibilidades de fabricação são fundamentais para o custo do produto.
- O Polipropeno é um material de fácil aquisição no mercado em diversas especificações,fácil logística, médio/baixo custo e pode ser encontrado com uma grande facilidade. Além disso, existem estudos técnicos, o que implica no maior conhecimento de suas propriedades e respostas devido ao seu manuseio e operação.
- ASTM D1998-06

Matriz de decisão do material
Critérios | Peso | Polipropileno | Aço Inox 316 | Aço Duplex | Fibra de Vidro
Massa específica | 4 | 8 | 6 | 8 | 8
Preço | 8 | 8 | 5 | 4 | 6
Resistência mecânica | 6 | 8 | 9 | 10 | 8
Resistência à Corrosão | 10 | 9 | 9 | 9 | 9
Resultado | | 163 | 137 | 143 | 147

https://www.grainger.com/tps/pumps_chemical_compatibility.pdf

https://www.alpinatermoplasticos.com.br/pdf/TANQUES_QUIMICOS.pdf

Contator

1. Para o desenvolvimento do contador, não temos Normas ou regras técnicas específicas na literatura, no entanto a solução que vai está no contator é NAOH, então todo manuseio e armazenamento do material tem que está de acordo com a ABNT NBR 14725-2:2019.
2. Utilizando o Artigo [X] como base teórica , o autor utiliza o PVC como material para o contactor, por ser uma solução mais barata, mais leve e quimicamente compatível, como podemos ver na tabela abaixo.

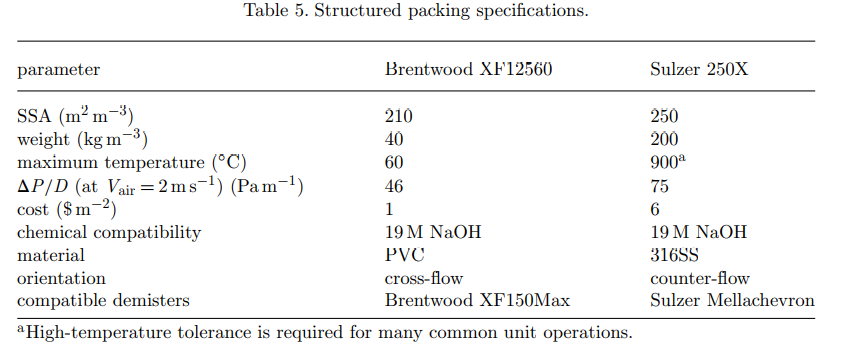
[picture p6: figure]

Brentwood XF12560 e Sulzer 250X são 2 soluções prontas da indústrias para Air contactor, mesmo que não sejam utilizadas , temos referencial teórico para a escolha dos materiais .

3. Para fazer a escolha do material também podemos usar a tabela abaixo, como usa o artigo [Y] .
A. Resistência ao Hidróxido de sódio
B. Tempo de vida maior que 20 anos
C. Baixa queda de pressão
D. Nao seja caro
E. Resistência à incrustação

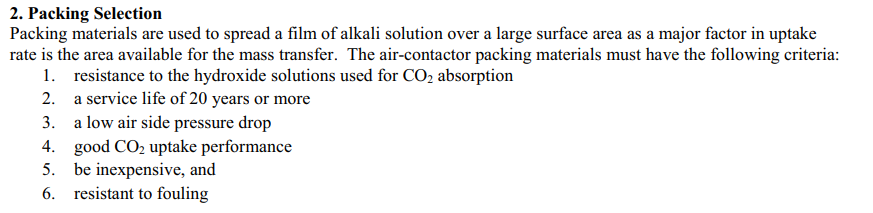
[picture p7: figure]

Artigo base

- (X)https://royalsocietypublishing.org/doi/10.1098/rsta.2012.0137
- [y] https://www.sciencedirect.com/science/article/pii/S1876610211003894?via%3Dihub

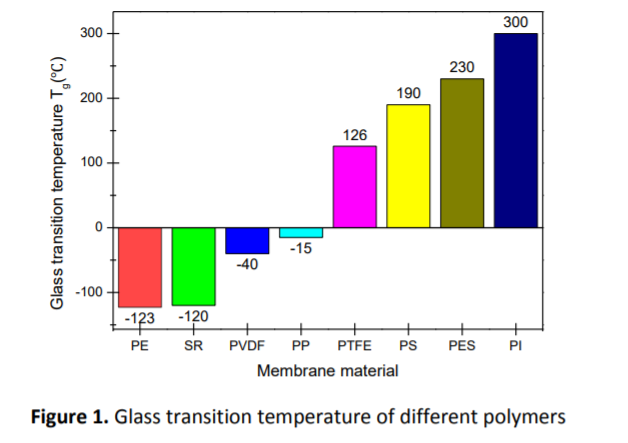
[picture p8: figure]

https://www.degruyter.com/document/doi/10.1515/gps-2017-0024/html

Cambier, Nicolas. Carbon dioxide capture using sodium hydroxide solution : comparison between an absorption column and a membrane contactor. Ecole polytechnique de Louvain, Université catholique de Louvain, 2017. Prom. : Luis Alconero, Patricia.

http://pdf.blucher.com.br.s3-sa-east-1.amazonaws.com/chemicalengineeringproceedings/cobeq2018/CO.067.pdf

https://journal.gnest.org/sites/default/files/Submissions/gnest_01343/gnest_01343_published.pdf

Tubulações e conexões

Para a escolha de materiais das tubulações, temos que levar em consideração que algumas partes do projeto vão ter contato com NaOH, outras não.

Para padronizar o projeto vamos escolher somente um tipo de material para as tubulações.

Temos que escolher um material de uma longa vida útil, resistente ao trabalho com temperatura acima de 45 graus, e ação do NAOH, baixo custo, fácil manutenção e usinagem .

Foi elaborada uma matriz de decisão X para escolha do material dos tubos, a tabela traz informações dos principais materiais que é utilizado para essa aplicação e o resultado mais adequado para o projeto, utilizando pesos que podem ser traduzidos em nível de prioridade.

Com o CPVC (Cloriploreto de Vinila Clorado) como resultado da matriz de decisão, podemos dizer que é a melhor escolha para o projeto, por ser um material de fácil instalação e manutenção, boa resistência mecânica ,confiável para transportes de produtos químicos a altas temperaturas, até 90 graus. Além de ser um produto de fácil aquisição no mercado.

ASTM F441

Matriz de decisão do material
Critérios | Peso | Polietileno | PVC | CPVC | Aço Inox
Incrustação/Perda de pressão | 7 | 8 | 7 | 8 | 7
Preço | 8 | 7 | 9 | 8 | 5
Resistência mecânica/Impactos/Pressão | 6 | 7 | 6 | 7 | 9
Resistência à Corrosão/Temperatura | 9 | 8 | 7 | 8 | 9
Massa específica | 7 | 9 | 8 | 8 | 5
Resultado | | 234 | 229 | 235 | 196

Referências

https://www.termomecanica.com.br/calculo-da-pressao-interna-de-trabalho-para-tubos

http://ftp.demec.ufpr.br/disciplinas/TM141/Conte%FAdos/aula09_USP.pdf

Bombas

- Temos 3 pontos onde temos que usar as bombas.
- Levar a substância do reservatório do carbonato de sódio para o reator,levar do reator para a centrífuga.
- Do reservatório de NAOH para o contator novamente.
- Para usar as bombas temos que levar alguns ponto importantes em consideração, preço, gasto energético, vazão por hora

Para os cálculos iniciais foram realizadas para definir os requisitos mínimos para a bomba

Como o projeto tem várias etapas, com diferentes substâncias e volumes a serem transportados para cada etapa, foram divididas as etapas onde tem a necessidade de utilizar a bomba, como indica na tabela X abaixo.

Número da fase | Descrição da fase /Estado
1 | Transferência da Solução aquosa da calha para alimentar o filtro (Líquido)
2 | Transferência do Reservatório de Ca Oh 2 para o reator (Sólido)
3 | Transferência do reator para Centrífuga (líquido)
4 | Transferência do Reservatório de NAOH para Contator (Líquido)

Tabela : numeração das fases para o cálculo inicia

Por termos vários tipos de etapas, e cada etapa precisa de uma vazão volumétrica, mostrado na tabela X , Como a vazão máxima acontece na etapa 3, onde temos uma vazão 5.02 L/min, sendo bem maior em comparação para outras etapas, lembrando que esse cálculo é caso o sistema trabalha somente por 1hora, caso o tempo de operação seja maior, a vazão volumétrica necessária diminui consideravelmente ao adicionar tempo.

Como mostrado na tabela X, há uma diferença de propriedades de viscosidade e massa específica, por causa das diversas misturas e substâncias, temos que levar em consideração diferentes propriedades para a escolha para a bomba de cada etapa. Como trabalhamos com misturas, não encontramos na literatura todas as propriedades físicas de cada um, por isso vamos levar em consideração para o cálculo do número de Reynolds e da perda de pressão e carga a substância mais presente na mistura.

Fase | Massa específica(KG/m3) | viscosidade dinâmica(Ns/m2) | Temperatura
1 | verificar
2 | 2240 | | 25
3 | 01.05 | 1.11 cp | 40
4 | 2.3 g/cm3 | 10.5 mpa.s | 30

Tabela. propriedades físicas

Dimensionamento das bombas (líquidos)

Como forma preliminar de dimensionar as bombas , temos uma série de pré-requisitos básicos para podermos fazer uma escolha, segundo o fabricante X(Schneider) podemos dimensionar fazendo os seguintes cálculos

AMT= ( AS + AR+PC) + 5%

AS: Altura de sucção

AR: Altura do recalque (Diferença da altura da bomba para o ponto mais alto)

PC: CT* Fpc%(Fator de perda de carga)

CT: Comprimento total da tubulação .

Sendo a altura do sistema na tabela a seguir.

Fase | Comprimento da tubulação | Diferença máxima de altura (m)
1 | A definir | A definir
2 | A definir | 1,5
3 | A definir | 0,2
4 | A definir | 3.5

http://cobeqic2019.com.br/trabalhosfinais/FTSP49.pdf

Fontes :

INCOMPLAST. POLIPROPILENO (PP). 2019. Disponível em: <https://incomplast.

com.br/polipropilenopp/>. Acesso em: 28 marco. 2020.

https://www.grabe.com.br/tanques-de-polipropileno.php

https://www.grabe.com.br/tanques_de_mistura.php

https://www.abntcatalogo.com.br/pdfview/viewer.aspx?Q=112BFBBEFA48709000EE1371B0469C52C31E81EBFB09BC64

MELLO, Lilian C.; CASTRO, Edmilson R. de; JERMOLOVICIUS, Luiz A.. METODOLOGIA EXPERIMENTAL PARA REAÇÕES GÁS-LÍQUIDO. Quím. Nova, São Paulo , v. 39, n. 5, p. 627-633, June 2016 . Available from <http://www.scielo.br/scielo.php?script=sci_arttext&pid=S0100-40422016000500627&lng=en&nrm=iso>. access on 29 Mar. 2021. https://doi.org/10.5935/0100-4042.20160036.

RIBEIRO, Leandro Sampaio Oliveira et al . Composição química e perdas fermentativas de silagem de cana-de-açúcar tratada com ureia ou hidróxido de sódio. R. Bras. Zootec., Viçosa , v. 39, n. 9, p. 1911-1918, set. 2010 . Disponível em <http://www.scielo.br/scielo.php?script=sci_arttext&pid=S1516-35982010000900008&lng=pt&nrm=iso>. acessos em 29 mar. 2021. https://doi.org/10.1590/S1516-35982010000900008.

ESTUDO DA ABSORÇÃO DE CO2 DE GASES EXAUSTOS DE USINAS TERMELÉTRICAS EM REATOR CILÍNDRICO CONTENDO SOLUÇÃO DE NaOH https://pantheon.ufrj.br/bitstream/11422/11526/1/monopoli10008950.pdf

http://lyceumonline.usf.edu.br/salavirtual/documentos/3117.pdf

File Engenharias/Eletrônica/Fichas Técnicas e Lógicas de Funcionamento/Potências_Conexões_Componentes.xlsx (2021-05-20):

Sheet: Folha1
componente | local | tensão V | corrente A | Potencia W | Quantidade | Potencia Total W | #VALUE! | Natureza | Valor Unitário | Valor Total
Disjuntor Motor GZ1E Schneider | Circuito de Potencia Estrela Triangulo | 220 |  |  | 4 |  | 0.000 | Controle | 239.96 | 959.84
Contator LC1D40A Schneider | Circuito de Potencia Estrela Triangulo | 220 |  |  | 4 |  | 0.000 | Controle | 575.93 | 2303.72
Contator LC1D40A Schneider | Circuito de Potencia Estrela Triangulo | 220 |  |  | 4 |  | 0.000 | Controle | 575.93 | 2303.72
Contator LC1D40A Schneider | Circuito de Potencia Estrela Triangulo | 220 |  |  | 4 |  | 0.000 | Controle | 575.93 | 2303.72
Temporizador RTW-ET WEG | Circuito de Potencia Estrela Triangulo | 220 | 0.080 | 17.600 | 4 |  | 0.320 | Controle | 165.00 | 660.00
Eletroválvula 1 | Conexão 6 | 24 | 9.900 | 237.600 | 1 | 237.600 | 9.900 | Atuador | 118.67 | 118.67
Eletroválvula 2 | Conexão 2 | 24 | 9.900 | 237.600 | 1 | 237.600 | 9.900 | Atuador | 118.67 | 118.67
Eletroválvula 3 | Conexão 4 | 24 | 9.900 | 237.600 | 1 | 237.600 | 9.900 | Atuador | 486.13 | 486.13
Eletroválvula 4 | Conexão 5 | 24 | 9.900 | 237.600 | 1 | 237.600 | 9.900 | Atuador | 118.67 | 118.67
Módulo Rele 16 canais Superior | central de controle dos acionamentos | 12 | 1.500 | 18.000 | 1 | 18.000 | 1.500 | Controle | 139.90 | 139.90
Módulo Rele 16 canais Inferior | central de controle dos acionamentos | 12 | 1.500 | 18.000 | 1 | 18.000 | 1.500 | Controle | 139.90 | 139.90
Sensor de Velocidade de rotação do ventilador |  | 12 | 0.100 | 1.200 | 2 | 2.400 | 0.200 | Sensor | 2970.00 | 5940.00
SENSOR DE NIVEL LA26M-40 |  | 12 | 0.417 | 5.000 | 4 | 20.000 | 1.667 | Sensor | 38.45 | 153.80
Servo Motor do Dispenser | Conexão 3 | 5 | 0.900 | 4.500 | 1 | 4.500 | 0.900 | Atuador | 38.20 | 38.20
Sensor Umidade DHT11 e temperatura ambiente |  | 5 | 0.001 | 0.007 | 1 | 0.007 | 0.001 | Sensor | 14.70 | 14.70
Sensor de EZO-CO2™ |  | 5 | 0.194 | 0.970 | 1 | 0.970 | 0.194 | Sensor | 1128.90 | 1128.90
Sensor Temperatura PT100 |  | 5 | 0.008 | 0.040 | 2 | 0.080 | 0.016 | Sensor | 274.92 | 549.84
Sensor de Pressão PXM309 |  | 5 | 0.020 | 0.100 | 1 | 0.100 | 0.020 | Sensor | 250.00 | 250.00
Sensor de nível e18-d80nk |  | 5 | 0.025 | 0.125 | 2 | 0.250 | 0.050 | Sensor | 33.20 | 66.40
Raspberry Pi 3 Modelo B+ |  | 5 | 0.600 | 3.000 | 1 | 3.000 | 0.600 | Comunicação | 429.90 | 429.90
MSP 430G2755 |  | 5.0 | 0.000180 | 0.001 | 2 | 0.002 | 0.00036 | Comunicação | 35.90 | 71.80
módulo NRF24L01 |  | 3.6 | 0.017 | 0.060 | 3 | 0.180 | 0.050 | Comunicação | 26.80 | 80.40

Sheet: Componentes Motor
Componentes Circuito Estrela-Triangulo
Componente | Legenda | Função
Disjuntor Motor GZ1E Schneider | Q1 | Responsavel pela proteção contra curto circuito e sobrecarga
Contator LC1D40A Schneider | K1 | Estebelecer contato
Contator LC1D40A Schneider | K2 | Estebelecer contato
Contator LC1D40A Schneider | K3 | Estebelecer contato
Temporizador RTW-ET WEG | D1 | Estabelecer contado após final de contagem
Relé OFF | OFF | Desenergizar o circuito por meio do controle da MSP
Relé ON | ON | Energizar o circuito por meio do controle da MSP

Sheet: Atuadores
 |  |  |  |  |  |  |  |  |  |  |  | Servo Motor MG996R
 |  |  |  |  |  | Modelo | Nome | Local | Tensão V | Corrente A | Potência W | Definição | Servo Motor de Alto Torque
Dispositivo | Identificação | Tensão V | Corrente A | Potencia W | Tipo de ligação | Rain Bird 100-PEB: 1" | Eletroválvula 1 | Conexão 6 | 24 | 9.9 | 237.6 | Tensão | 5V
Sistemas de Pressurização Série BPR-9 | Bomba1 | 220 | 0.5 | 120 | Monofásica | Rain Bird 100-PEB: 1" | Eletroválvula 2 | Conexão 2 | 24 | 9.9 | 237.6 | Corrente | 0.9 A
Sistemas de Pressurização Série BPR-9 | Bomba2 | 220 | 0.5 | 120 | Monofásica | Rain Bird 150-PEB: 1 1/2" | Eletroválvula 3 | Conexão 4 | 24 | 9.9 | 237.6 | Potência | 4.5 W
Sistemas de Pressurização Série BPR-9 | Bomba3 | 220 | 0.5 | 120 | Monofásica | Rain Bird 100-PEB: 1" | Eletroválvula 4 | Conexão 5 | 24 | 9.9 | 237.6 | Torque | 9.4 Kg/f
Sistemas de Pressurização Série BPR-9 | Bomba4 | 220 | 0.5 | 120 | Monofásica
Motobombas Autoaspirantes Série BCA-40 1 1/2 | Bomba5 | 220 | 10.0 | 2207 | Monofásica
Motobombas Centrífugas Monoestágio Série BCR-2000 | Bomba6 | 220 | 3.3 | 736 | Monofásica
 |  |  | /

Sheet: Folha3
Dispositivos | Potencia | Tensão | Corrente | Frequencia
Lm2596 Conversor Regulador Tensão Step Down 12V P/ 5V | 15 W | 5V | 3A | -
Fonte de Alimentação Chaveadas - S-100-12 | 102W | 12V | 8.5A | -
Cód. 9560 Transformador Trafo Hunion | 480W | 24V | 20A | 60 Hz
Transformador
Dispositivo | Potencia | Tensão | Corrente | Frequencia
Cód. 9560 Transformador Trafo Hunion | 480W | 24V | 20A | 60 Hz
 |  |  |  | apendece M termoquimica

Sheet: Conexões
 |  | Conexões lógicas módulo relé 16 canais e MSP |  |  |  | Conexões MSP
 |  | Pinos Logicos Módulo Relé | Relé | Atuador | Pino MSP | Pino MSP | Pino Elemento | Elemento
 |  | 1 | Relé ON 1 | Exaustor 1 | P3.0 | P1.5 | SCK
 |  | 2 | Relé OFF 1 | Exaustor 1 | P3.1 | P1.6 | MISO
 |  | 3 | Relé ON 2 | Exaustor 2 | P3.2 | P1.7 | MOSi
Caracteristicas Técnicas |  | 4 | Relé OFF 2 | Exaustor 2 | P3.3 | P2.0 | CE
Numero de canais | 16 | 5 | Relé ON 1 | Motor Pás Reator | P3.4 | P2.1 | CSN
Carga nominal | 10A 250VAC/ 10A 125VAC/ 10A 30VDC/ 10A 28VDC | 6 | Relé OFF 1 | Motor Pás Reator | P3.5 | P2.2 | IRQ
Voltagem nominal | 12V | 7 | Relé ON 1 | Motor Centrífuga | P3.6 | P2.3 |  | Eletroválvula 1
Controle lógico | 5V | 8 | Relé OFF 1 | Motor Centrífuga | P3.7 | P2.4 |  | Eletroválvula 2
Dimensões totais | 18x9x1,8cm | 9 | Relé BombRec1 | Bomba de Recirculação 1 | P4.2 | P2.5 |  | Eletroválvula 3
Compatibilidade | Compatível com MSP, Raspberry Pi, AVR, ARM, Arduino | 10 | Relé BombRec2 | Bomba de Recirculação 2 | P4.3 | P2.6 |  | Eletroválvula 4
Tensão de carga | Controle AC/DC | 11 | Relé Bomb1Res2 | Bomba Contator Esquerdo - Reservatório 2 | P4.4 | P2.7 |  | Eletroválvula 5
Interface com usuário | LED indicador de status | 12 | Relé Bomb2Res2 | Bomba Contator Direito - Reservatório 2 | P4.5 | P3.0 | Relé ON 1 | Exaustor 1
 |  | 13 | Relé BombRes3 | Bomba Reservatório 3 | P4.6 | P3.1 | Relé OFF 1 | Exaustor 1
 |  | 14 | Relé BombCent | Bomba Reator - Centrífuga | P4.7 | P3.2 | Relé ON 2 | Exaustor 2
 |  | 15 | - | - | - | P3.3 | Relé OFF 2 | Exaustor 2
 |  | 16 | - | - | - | P3.4 | Relé ON 1 | Motor Pás Reator
 |  |  |  |  |  | P3.5 | Relé OFF 1 | Motor Pás Reator
 |  |  |  |  |  | P3.6 | Relé ON 1 | Motor Centrífuga
 |  | Conexões lógicas módulo relé 6 canais e MSP |  |  |  | P3.7 | Relé OFF 1 | Motor Centrífuga
 |  | Pinos Logicos Módulo Relé | Relé | Atuador | Pino MSP | P4.2 | Relé BombRec1 | Bomba de Recirculação 1
 |  | 1 | Relé EV1 | Eletroválvula 1 | P2.3 | P4.3 | Relé BombRec2 | Bomba de Recirculação 2
 |  | 2 | Relé EV2 | Eletroválvula 2 | P2.4 | P4.4 | Relé Bomb1Res2 | Bomba Contator Esquerdo - Reservatório 2
 |  | 3 | Relé EV3 | Eletroválvula 3 | P2.5 | P4.5 | Relé Bomb2Res2 | Bomba Contator Direito - Reservatório 2
 |  | 4 | Relé EV4 | Eletroválvula 4 | P2.6 | P4.6 | Relé BombRes3 | Bomba Reservatório 3
 |  | 5 | Relé EV5 | Eletroválvula 5 | P2.7 | P4.7 | Relé BombCent | Bomba Reator - Centrífuga
 |  | 6 | - | - | -

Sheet: Conexões MSP
Conexões MSP Superior |  |  | Conexões MSP Inferior |  |  | [Superiror] Conexões lógicas módulo relé 16 canais e MSP |  |  |  | [Inferior] Conexões lógicas módulo relé 16 canais e MSP
Pino MSP | Pino Elemento | Elemento | Pino MSP | Pino Elemento | Elemento | Pinos Logicos Módulo Relé | Relé | Atuador | Pino MSP | Pinos Logicos Módulo Relé | Relé | Atuador | Pino MSP
AVCC |  |  | AVCC |  |  | 1 | Relé ON 1 | Exaustor 1 | P3.0 | 1 | Relé ON 1 | Motor Pás Reator | P3.0
AVSS |  |  | AVSS |  |  | 2 | Relé OFF 1 | Exaustor 1 | P3.1 | 2 | Relé OFF 1 | Motor Pás Reator | P3.1
RST |  |  | RST |  |  | 3 | Relé ON 2 | Exaustor 2 | P3.2 | 3 | Relé ON 1 | Motor Centrífuga | P3.2
TEST |  |  | TEST |  |  | 4 | Relé OFF 2 | Exaustor 2 | P3.3 | 4 | Relé OFF 1 | Motor Centrífuga | P3.3
P1.0 |  |  | P1.0 |  |  | 5 | Relé BombRec1 | Bomba de Recirculação 1 | P3.4 | 5 | Relé BombRes3 | Bomba Reservatório 3 | P3.4
P1.1 |  |  | P1.1 |  |  | 6 | Relé BombRec2 | Bomba de Recirculação 2 | P3.5 | 6 | Relé BombCent | Bomba Reator - Centrífuga | P3.5
P1.2 |  |  | P1.2 |  |  | 7 | Relé Bomb1Res2 | Bomba Contator Esquerdo - Reservatório 2 | P3.6 | 7 | Relé EV2 | Eletroválvula 2 | P3.6
P1.3 |  |  | P1.3 |  |  | 8 | Relé Bomb2Res2 | Bomba Contator Direito - Reservatório 2 | P3.7 | 8 | Relé EV3 | Eletroválvula 3 | P3.7
P1.4 |  |  | P1.4 |  |  | 9 | Relé EV1 | Eletroválvula 1 | P4.1 | 9 | Relé EV4 | Eletroválvula 4 | P4.0
P1.5 | SCK | Módulo RF | P1.5 | SCK | Módulo RF | 10 | - | - | - | 10 | - | - | -
P1.6 | MISO | Módulo RF | P1.6 | MISO | Módulo RF | 11 | - | - | - | 11 | - | - | -
P1.7 | MOSi | Módulo RF | P1.7 | MOSi | Módulo RF | 12 | - | - | - | 12 | - | - | -
P2.0 | CE | Módulo RF | P2.0 | CE | Módulo RF | 13 | - | - | - | 13 | - | - | -
P2.1 | CSN | Módulo RF | P2.1 | CSN | Módulo RF | 14 | - | - | - | 14 | - | - | -
P2.2 | IRQ | Módulo RF | P2.2 | IRQ | Módulo RF | 15 | - | - | - | 15 | - | - | -
P2.3 |  |  | P2.3 |  |  | 16 | - | - | - | 16 | - | - | -
P2.4 |  |  | P2.4
P2.5 |  |  | P2.5
P2.6 |  |  | P2.6
P2.7 |  |  | P2.7
P3.0 | Relé ON 1 | Exaustor 1 | P3.0 | Relé ON 1 | Motor Pás Reator
P3.1 | Relé OFF 1 | Exaustor 1 | P3.1 | Relé OFF 1 | Motor Pás Reator
P3.2 | Relé ON 2 | Exaustor 2 | P3.2 | Relé ON 1 | Motor Centrífuga
P3.3 | Relé OFF 2 | Exaustor 2 | P3.3 | Relé OFF 1 | Motor Centrífuga
P3.4 | Relé BombRec1 | Bomba de Recirculação 1 | P3.4 | Relé BombRes3 | Bomba Reservatório 3
P3.5 | Relé BombRec2 | Bomba de Recirculação 2 | P3.5 | Relé BombCent | Bomba Reator - Centrífuga
P3.6 | Relé Bomb1Res2 | Bomba Contator Esquerdo - Reservatório 2 | P3.6 | Relé EV2 | Eletroválvula 2
P3.7 | Relé Bomb2Res2 | Bomba Contator Direito - Reservatório 2 | P3.7 | Relé EV3 | Eletroválvula 3
P4.0 | Motor Dispenser | Dispenser | P4.0 | Relé EV4 | Eletroválvula 4
P4.1 | Relé EV1 | Eletroválvula 1 | P4.1
P4.2 |  |  | P4.2
P4.3 |  |  | P4.3
P4.4 |  |  | P4.4
P4.5 |  |  | P4.5
P4.6 |  |  | P4.6
P4.7 |  |  | P4.7

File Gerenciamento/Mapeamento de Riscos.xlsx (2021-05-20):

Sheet: Riscos do Sistema
ID | Risco | Descrição | ID | Causa | Efeito | Como Prevenir | Como Corrigir ou Mitigar
R1 | Queda de energia/interrupção da alimentação elétrica do sistema | Interrupção da alimentação do sistema causa o mau funcionamento dos motores, e consequentemente dos equipamentos essenciais (ventiladores, bombas, reator); Dessa forma o sistema não entrega a funcionalidade; | R1 | Falha no sistema elétrico | - Equipamentos que precisam de alimentação param de funcionar e o sistema não entrega o que foi proposto. - Queima e danificação de componentes eletro-eletrônicos | Dimensionar corretamente os condutores e os componentes eletro-eletrônicos. fazer inspeções periódicas ao sistema. | Fonte de energia ininterrupta (nobreak) na central de comunicação
R2 | Falha no sistema de amazenamento de hidróxido de sódio | Tanque aonde se encontra a Soda Romper/Quebrar etc.. ocasionando vazamento de soda no ambiente | R2 | Armazenamento incorreto da substância, disturbios externos e internos que ultrapasse a capacidade fisica do tanque. | Acidente de trabalho; contaminação ambiental. | Dimensionamento correto do reservatório, inspeções periódicas | Substituição do elemento danificado; neutralização da substância vazada
R3 | Mau funcionamento da bomba | Bomba não funcionar da forma correta | R3 | Falhas elétrica ou falhas mecânicas e hidraulicas | O fluido não chega corretamente ao destino; paralização do sistema | Dimensionar corretamente a bomba; monitorar o funcionamento dispositivo; manutenções preventivas; inspeções periódicas; | Manutenção corretiva: substituição dos componentes ou do equipamento por completo;
R4 | Mau funcionamento do ventilador | Ventilador não funcionar da forma correta | R4 | Falhas elétricas, falhas mecânicas, intempéries climáticas | A vazão de ar é comprometida | Dimensionar corretamente o ventilador;manutenções preventivas; inspeções periódicas; | Manutenção corretiva: substituição dos componentes ou do equipamento por completo;
R5 | Superaquecimento da estrutura | Elevação da temperatura além do previsto devido a reações químicas, podendo levar ao aquecimento do local ao redor e riscos de queimadura | R5 | Aumento de temperatura pelas reações químicas | Acidentes | Monitoramento constante da temperatura | Atuadores responsáveis pela diminuição da temperatura
R6 | Elevação de pressão | Elevação da pressão além do previsto devido a reações químicas | R6 | Elevação da pressão pela liberação de gases nas reações químicas | Riscos de deformação da estrutura e explosão | Monitoramento constante da pressão | Informar responsáveis para interromper o uso
R7 | Queima ou falha nos equipamentos eletrônicos | Possível queima de equipamentos eletrônicos | R7 | Falhas elétricas, uso incorreto ou problemas de fabricação |  | Dimensionamento correto dos dispositivos e sistemas eletrônicos; inspeções periódicas. | Substituição dos componentes
R8 | Dificuldade de comunicação entre raspberry e o servidor | dificuldade do envio ou recepção dos dados | R8 | servidor fora do ar; interferência eletromagnéticas; falhas elétricas | Não há troca de dados parcialmente ou por completo | seguir os protocolos e padrões de comunicação corretamente; assegurar a não interferência eletromagnéticas entre a Raspbarry e o servidor
R9 | Falta de confiabilidade dos dados | Falha nos tratamentos de dados para envio e recebimento durante a comunicação entre componentes, o controlador e o sistema | R9 | interferências eletromegnéticas; sensores não calibrados; mau funcionamento do circuito condicionador de sinais | envio de dados incorretos | Dimensionamento correto dos dispositivos; calibração periodica | reenviar os dados; substituição dos eletementos inconsistentes; monitorar coerencia dados recebidos
R10 | Incompatibilidade dos resultado obtidos na simulação com a realidade | Por se tratar de um projeto que não será implementado, todos os testes serão feitos por simulação, o que pode não condizer com a realidade | R10 | eventos estocásticos característicos da realidade; não mapear parametros fundamentais para uma simulação mais realista | O projeto pode apresentar falhas não previstas em simulação | Buscar simular condições extremas de aplicação | reparar os danos e redimensionar o sistema incoerente
R11 | Danos no sensoriamento | As condições causadas pelas reações podem danificar a integridade dos sensores | R11 | Instalação inadequada do sensor, escolha de um sensor inadequado para operar em condições mais adversas. | Coleta de dados prejudicada. Sistema de segurança comprometido caso haja desregulação na temperatura e pressão. | Escolher sensores que operem nas situações desejadas e instalá-los de modo que sofram menos dano possível. E calibração regular do sensor e verificação das condições de uso. | Equipe técnica especializada realizando a troca do sensor e corrigindo os erros cometidos.
R12 | Entupimento do filtro | Filtro aonde capta o CO2 pode entupir por causa da umidade e particulas solidas no ar | R12 | Acumulo de particulas sólidas | Podera afetar toda a codeia de produçao, podendo parar todo o processo. | Instalar a estrutura em lugar arejado aonde é possivel ter controle do ar que entra nos filtros; inspeções periodicas | Determinar janelas de limpeza no equipamento
R13 | Ropimento de tubulação | Tubulaçoes rompem e o fluxo é interropido | R13 | Por causa das vibrações causadas pelas bombas,centrifuga,reator as tubulaçoes que ligam o sistema podem romper impedindo o fluxo do sistema; | Toda a cadeia de produção pode ser interropida; já que um sistema não vai alimentar o outro. | Usar tubulações que possam suportar tais vibrações, não usar materiais rígidos que não abosorva as vibrações | Substituir os elementos danificado
R14 | A solução de NaOH reagir com algum elemento estrutural externo | Rompimento da reservatório ou tubulação aonde passa o NaOH e ao reagir cause dano estrutural | R14 | Mau dimensionamento dos componentes estruturais e isolamento | Estrutura pode reagir e perder sua função estrutural podendo causar falha ou mau funcionamento das bombas, reatore e Centrifuga. | Proteger toda a superficie externa da estrutura com algum material inerte para não reagir diretamente | Limpar externamente todos os equipamentos para não ter o risco de reagir por um longo periodo de tempo; substituir os elementos estruturais danificados
R15 | A solução de NaOH reagir com algum elemento estrutural interno | Componentes interno das bombas, reator e resevatórios falharem ao ponto de não manterem a eficiência | R15 | Falha do isolamento do material interno; dimensionamento incorreto do elemento estrutural | Etapas dos processo podem perder eficacia ou sistema parar completamente | Proteger toda a superficie interna da estrutura com algum material inerte; Realizar limpezas e manutenções dentro do tempo especificado por cada fabricante | substituição dos elementos danificados

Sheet: Riscos de Projeto
ID | Risco | Descrição | Causa | Efeito | Como Prevenir | Como Corrigir
 | Evasão de membros | Membro sair do projeto ao longo do semestre | Podem ser varias causas, desde da vida pessoal ao desistir de fazer a materia para dar prioridade a outra atividade | Aumento da carga de trabalho para outros membros | Dividir bem as tarefas para nenhum membro ficar sobrecarregado
 | Escopo mal definido | Projeto não está bem definido, resutando em falta de estudo de areas importantes | Falta de compremetimento do grupo nos estudos previos para definir o escolpo da atividade
 | Falha de comunicação interna
 | Falha de comunicação externa
 | Falta de comprometimento de integrantes dos time
 | Mudanças no escopo do projeto | Projeto mudar de escolpo no meio do semestre | Dificuldade encontrada para realizar estudos e falta de material na biblioteca para embasamento teorio | Necessidade de realizar outro

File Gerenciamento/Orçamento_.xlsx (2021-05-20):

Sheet: Eletrônica.
Item | Quantidade | Valor Unit. | Valor Total | Fornecedor
Sensor de Temperatura GY-906 MLX90614 | 3 | 42.18 | 126.54 | MultilógicaShop
Sensor de Dióxido de Carbono MG811 | 1 | 114.81 | 114.81 | AliExpress
Sensor De Nivel La26m-40 | 6 | 38.45 | 230.7 | Mercado Livre
Sensor de Umidade do Ar HR202L com Relé | 1 | 31.86 | 31.86 | Destrinchando na Elétrica
Sensor PH Módulo PH4502C + PH Eletrodo | 1 | 182.9 | 182.9 | Saravati Materiais Técnicos
Sensor de Pressão Analógico XMLG400D21 | 1 | 301.99 | 301.99 | Mercado Livre
Sensor de Fluxo AWM720 | 1 | 794.92 | 794.92 | Mouser Electronics
nRF24L01 | 3 | 24.99 | 74.97 | Mercado Livre
Raspberry Pi 3 Model B+ Plus Pi3 1.4ghz Wifi 5ghz | 1 | 399 | 399 | Mercado Livre
Raspberry PI 3 Model B Quadcore 1.2ghz 1Gb Wifi Bluetooth | 1 | 299.89 | 299.89 | Mercado Livre
Módulo Ads1115 Adc 16 Bits | 1 | 38.9 | 38.9 | Mercado Livre
Msp430g2553 Circuito Integrado M430g2553 | 1 | 29.99 | 29.99 | Mercado Livre
 |  |  | 2626.47

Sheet: Estrutura
Item | Quantidade | Valor Unit. | Valor Total

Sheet: Energia
Item | Quantidade | Valor Unit. | Valor Total

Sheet: Software
Item | Quantidade | Valor Unit. | Valor Total

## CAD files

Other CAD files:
Engenharias/Estruturas/CAD FINAL/Aspessor.CATPart
Engenharias/Estruturas/CAD FINAL/Bomba Contator.CATPart
Engenharias/Estruturas/CAD FINAL/Bomba NaOH.CATPart
Engenharias/Estruturas/CAD FINAL/Bomba Reator_Centri.CATPart
Engenharias/Estruturas/CAD FINAL/Cabo de aco.CATPart
Engenharias/Estruturas/CAD FINAL/Calha .CATPart
Engenharias/Estruturas/CAD FINAL/Cerca.CATPart
Engenharias/Estruturas/CAD FINAL/Contator.CATProduct
Engenharias/Estruturas/CAD FINAL/Duto Mestre.CATPart
Engenharias/Estruturas/CAD FINAL/Eletrovalvula 2.CATPart
Engenharias/Estruturas/CAD FINAL/Eletrovalvula.CATPart
Engenharias/Estruturas/CAD FINAL/Escada.CATPart
Engenharias/Estruturas/CAD FINAL/Estrutura Externa.CATPart
Engenharias/Estruturas/CAD FINAL/Fechamento.CATPart
Engenharias/Estruturas/CAD FINAL/Filtro.CATPart
Engenharias/Estruturas/CAD FINAL/Joelho 112.CATPart
Engenharias/Estruturas/CAD FINAL/Joelho 34.CATPart
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

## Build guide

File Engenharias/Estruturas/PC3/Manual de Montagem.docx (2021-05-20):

Primeiramente uma estrutura externa deve ser montada a base de soldas de tubos de 200x200mm para as vigas horizontais e verticais e para as treliças uma sessão de 130x130mm. Essa estrutura serve para suportar o peso dos componentes provenientes do sistema de absorção de ar. Para ajudar em posteriores manutenções é necessário a instalação de uma escada lateral, possibilitando assim o acesso do usuário ao andar de cima para reabastecimento ou reparos.

Em sequência é necessário fazer a fixação do duto mestre nas treliças. Uma extremidade deve ser chanfrada para proteger o exaustor de possíveis chuvas, a mesma fica soldada na parte estrutural externa e a outra extremidade deve ser soldada nas paredes do módulo de absorção de ar. Este duto tem o intuito de restringir o fluxo de ar para aquele determinado espaço e suportar o exaustor, que fica a 5 mm da extremidade chanfrada, antes da instalação do mesmo é necessário a implementação de um encoder para monitoramento da velocidade de rotação do motor do exaustor.

Após a montagem do duto mestre e do exaustor na parte interna do duto, é necessário adicionar na outra extremidade próxima ao módulo de ar um sensor de medição de CO2 para que possamos analisar a queda/purificação do ar.

Dentro do módulo de absorção de ar, é implementado um sistema de recirculação para auxiliar na captura do CO2. Este sistema consiste no uso de um filtro de PVC encharcado de NaOH para ajudar na coleta do CO2 do ar que passa pelo filtro, essa reação que acontece gera uma solução aquosa que escorre para uma calha que fica situada abaixo do filtro, que é suspenso por uma mesa de elevação. Quando essa solução aquosa cai na calha, o sistema de recirculação entra em ação fazendo a solução voltar para o filtro, através de uma bomba conectada a tubos de ¾” que retira o líquido da calha e molha o filtro em um raio igual a 1 metro através da instalação de um aspersor.

Ao lado do módulo de absorção de ar também é necessário o uso de outra bomba para levar a solução aquosa diretamente um reservatório específico de 250 litros feito de polietileno que é monitorado por sensores de nível alto/baixo instalados por furos M12 na extremidade mais alta e mais baixa do reservatório avisando o operador de quando deve prosseguir para a próxima fase. Somente quando este reservatório está cheio, é quando começa o processo de tratamento do CO2 captado.

Através do acionamento de uma eletroválvula, essa solução aquosa é levada para um reator químico por tubos de ¾ e junto dessa substância é usado um aditivo de Hidróxido de Cálcio, que fica situado em um reservatório localizado no teto da estrutura. Este reservatório deve ser instalado exatamente acima do reator, para facilitar o transporte da substância que se encontra no estado sólido e monitorado por um sensor de nível infravermelho, que fica situado bem ao meio do reservatório, para que possa reabastecer o mesmo antes mesmo de ficar completamente vazio. A saída dessa substância é controlada por um servo motor que é instalado na válvula de saída do reservatório.

No térreo do ambiente, o único componente que tem lugar predefinido é o reator, pois o mesmo deve estar obrigatoriamente situado abaixo do reservatório de hidróxido de cálcio. Os demais componentes são dispostos de forma ergonômica para que possibilite o trânsito de pessoas no interior. No reator deve ser feito furos M12 para instalação de um poço termométrico e um sensor de pressão, para monitorarmos as variações da reação que está ocorrendo internamente

Quando as substâncias são processadas pelo reator, o produto resultante sai do reator através da abertura de outra eletroválvula. Os tubos nessa fase são de exatamente 1.1/2” justamente por causa da viscosidade do líquido proveniente da reação e são bombeados para um decantador centrífugo.

No decantador centrífugo é onde acontece a divisão entre o sólido e o líquido do produto gerado da reação. A própria centrífuga possui um motor que atua nessa separação e também na vazão de saída de ambos os materiais por orifícios diferentes através de tubos de 1.1/2” que são suspensos por cabos de aço preso ao teto, para evitar empeno dos tubos e então chegando ao produto final proveniente da captura de CO2, que é o Carbonato de Cálcio.

No outro orifício, a centrífuga leva o NaOH para seu respectivo reservatório, onde o mesmo é reutilizado no sistema, reservatório este que é monitorado por sensores de nível baixo/alto instalados por furos M12 na lateral do mesmo. Ao lado dos sensores de nível, também é necessário o uso de um poço termométrico para monitoramento das variações de temperatura. Através de uma bomba, esse NaOH volta para o módulo de absorção controlado por uma eletroválvula logo após a bomba. Os tubos nessa fase devem ser fixados com cabos de aço ao teto para que continuem rígidos e retos sem empenar, pois, os tubos ficam suspensos sabendo que a centrífuga deve ser colocada em uma mesa

Ao retornar o NaOH para o módulo de absorção, o mesmo já está pronto para reação do ar novamente, reiniciando o ciclo de captura do CO2 e todo esse sistema é monitorado por uma sala de gerenciamento situada frente os componentes

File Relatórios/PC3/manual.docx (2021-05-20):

1. Segurança de Operação

2. Recomendações

- perda de água

2 Introdução

- apresentar o produto
- Imagens vista isométrica e imagem mostrando todos os componentes do piso 1 e piso 2

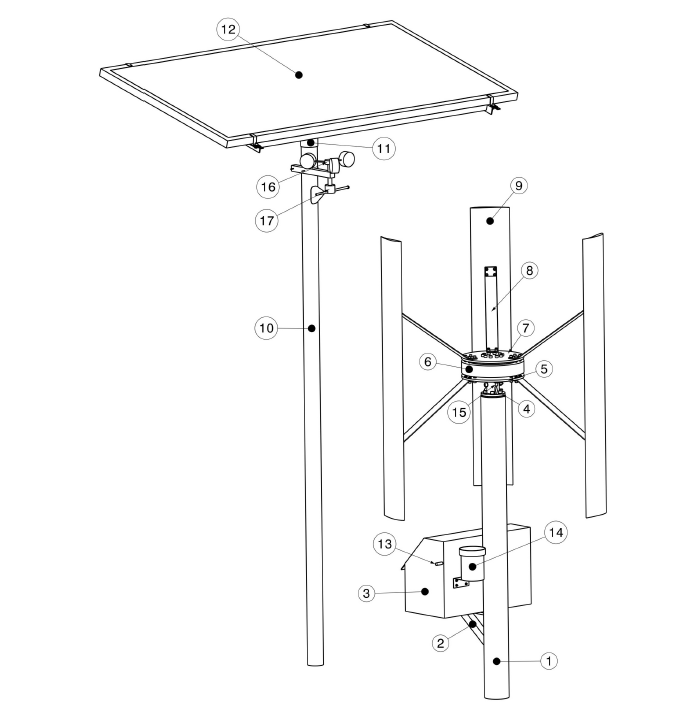
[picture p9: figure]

Mostrar cada componente separados, tubos e bombas

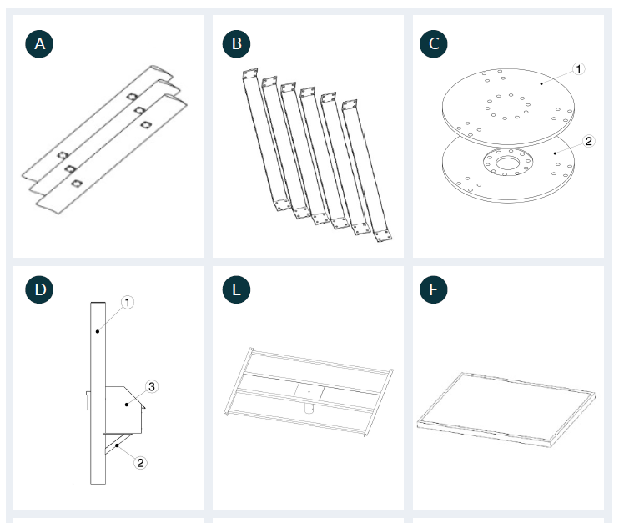
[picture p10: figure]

- Tabela com indices e nomes dos componentes

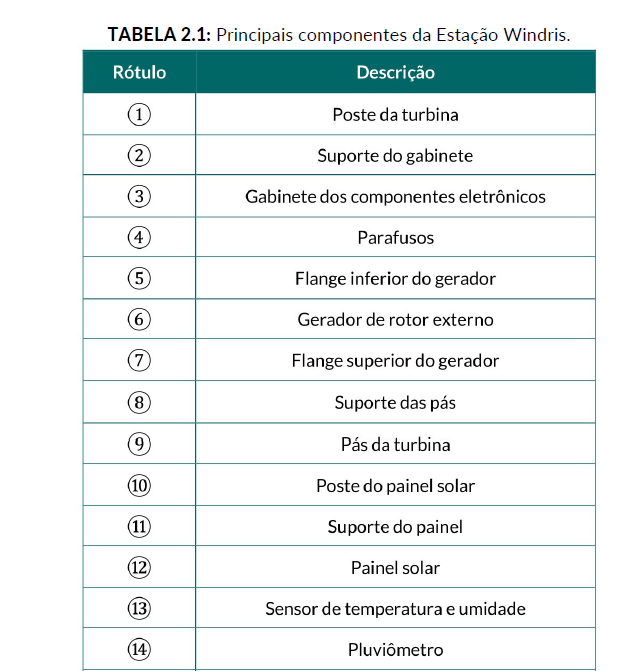
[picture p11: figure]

Mostrar componentes do contator

- Tabela com indices e nomes dos componentes sistema de absorção
- Tabela com características dos componetes

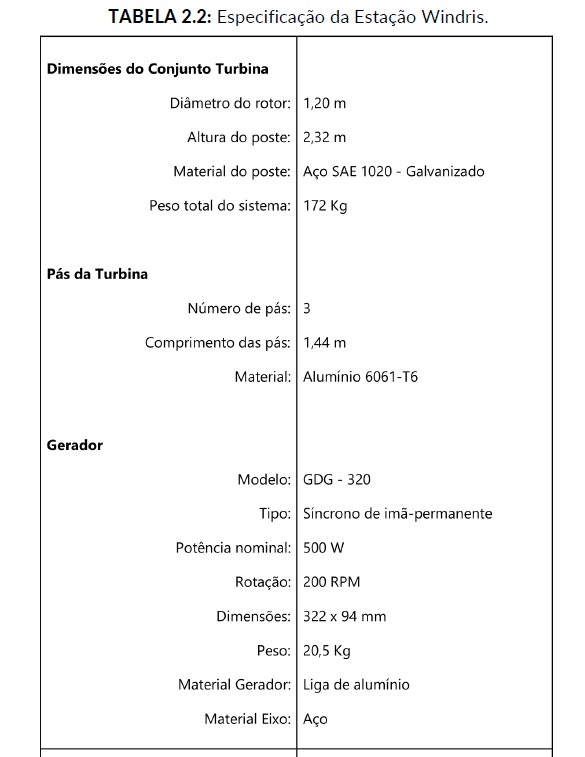
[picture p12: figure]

mostrar componentes eletronicos, sensores, atuadores, placas e cabos

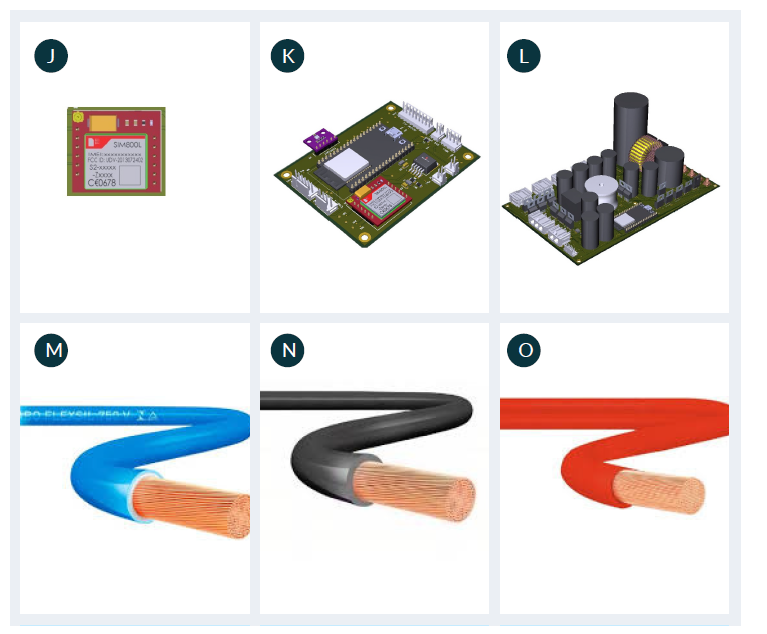
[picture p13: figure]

- Tabela com índices e nomes dos componentes sistema de absorção

3. Preparativos para Montagem e Instalação

- imagem da estrutura externa(grade escada, sala de controle)
- falar da estrutura externa

4. Montagem e Instalação

- Ferramentas para montagem
  - tipos de solda
  - Cola
  - .Reduções
  - …

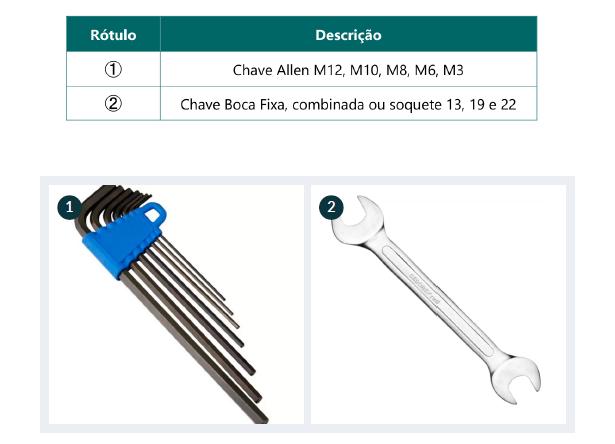
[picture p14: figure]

- Montagem dos componentes
  - Processo de fabricação do Sistema de absorção de co2
  - montagem do sistema estrutura
    - Disposição dos componentes estruturais
    - Forma de conexão dos tubos
    - disposição dos componentes eletrônicos na estrutura
    - sistemas de cabos
      - piso 1
      - piso 2

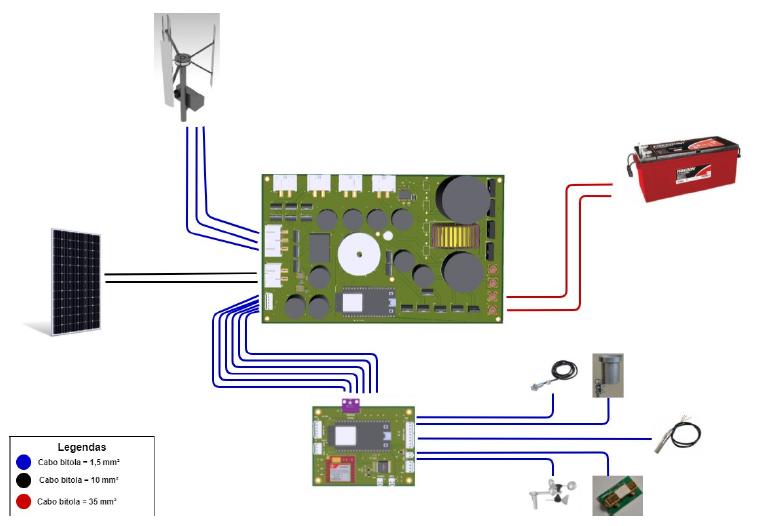
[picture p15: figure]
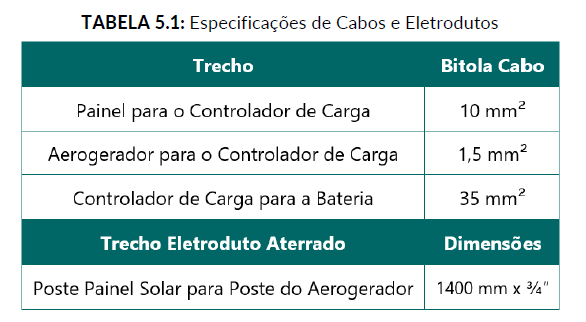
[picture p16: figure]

5 Operação

- Software

6.Manutenção

Preventiva

- de cada componte

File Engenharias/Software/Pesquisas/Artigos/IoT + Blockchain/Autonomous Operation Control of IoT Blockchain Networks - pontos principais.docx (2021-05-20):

IoT + Blockchain = Uma arquitetura blockchain pode ser usada para construir redes IoT altamente confiáveis. O livro razão(conceito de blockchain) compartilhado e a validação de dados aberta entre os usuários garantem uma segurança de dados extremamente alta.

Limitações dessa integração:

- Como as redes blockchain sem permissão geral, normalmente visam nós de rede de alto desempenho com poder de computação suficiente, um nó blockchain com baixo poder de computação e memória, como um sensor / atuador IoT, não pode operar em um blockchain como um nó totalmente funcional.
- consumo de energia, outro problema inerente ao blockchain
- nós dinâmicos da rede ao longo do tempo em sistemas iot

Solução:

- blockchain leve(ambiente de desenvolvimento hyperledger, porém só uma nova estrutura de blockchain não foi suficiente)
- configuração de rede IoT blockchain dinâmica por meio de clustering profundo (deep clustering)
- dApp reduzido (aplicativo distribuído) espalhando por meio de classificação de nó de rede neural + gráfos (GNN) -> essa é mais eficiente que a anterior

Referência

- https://www.mdpi.com/2079-9292/10/2/204/htm#

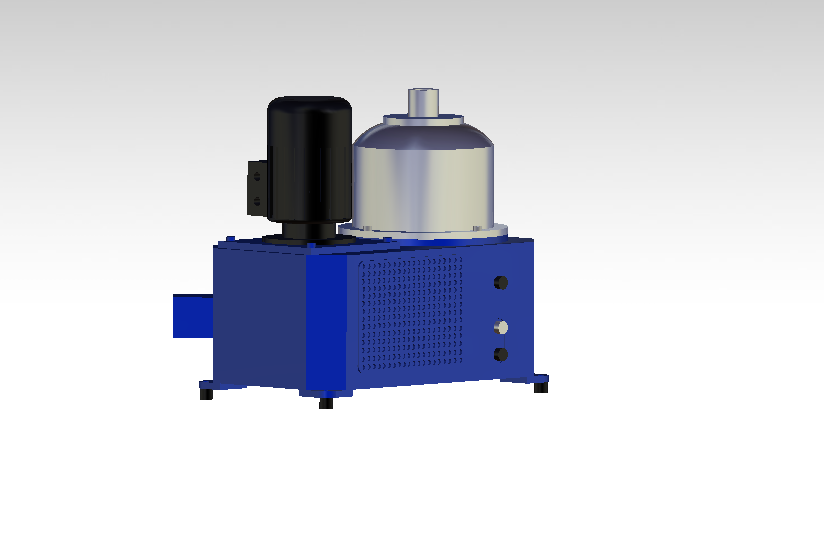
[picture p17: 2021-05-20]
Engenharias/Estruturas/PC3/Prints FINAIS/Centrifuga.png

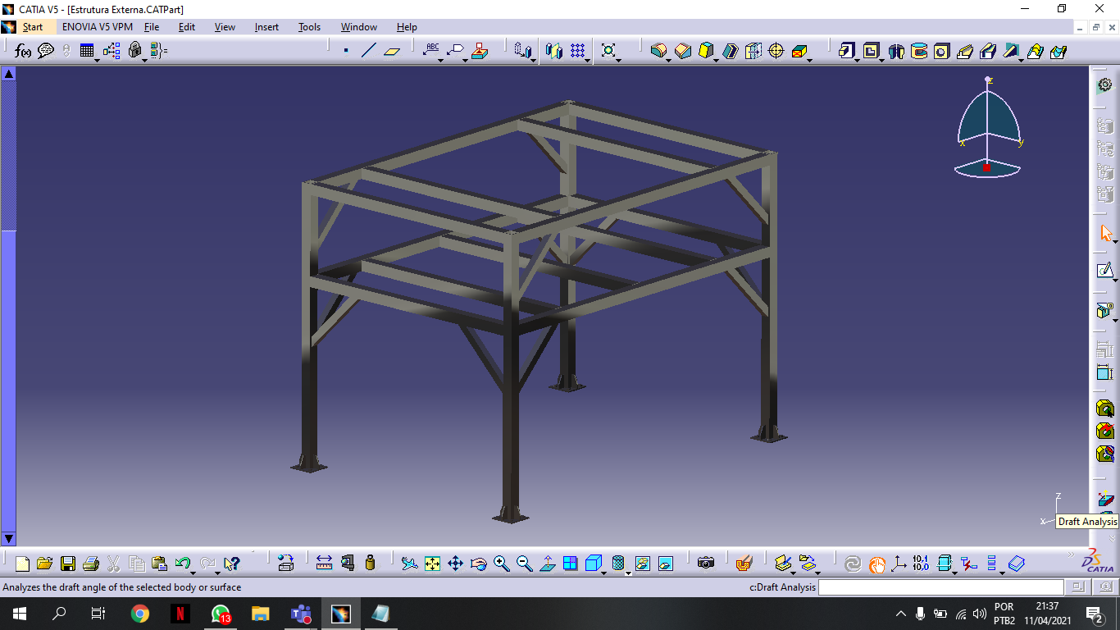
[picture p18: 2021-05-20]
Engenharias/Estruturas/PC2/PRINTS DO CAD - PC2/ESTRUTURA EXTERNA.png

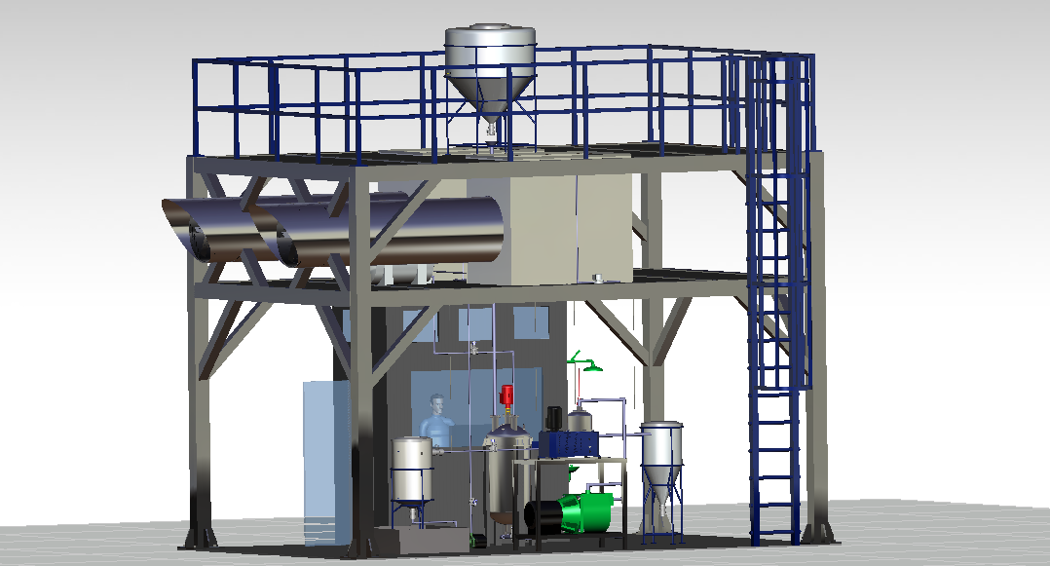
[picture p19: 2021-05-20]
Engenharias/Estruturas/PC3/Prints FINAIS/Isometrica Atualizada.png

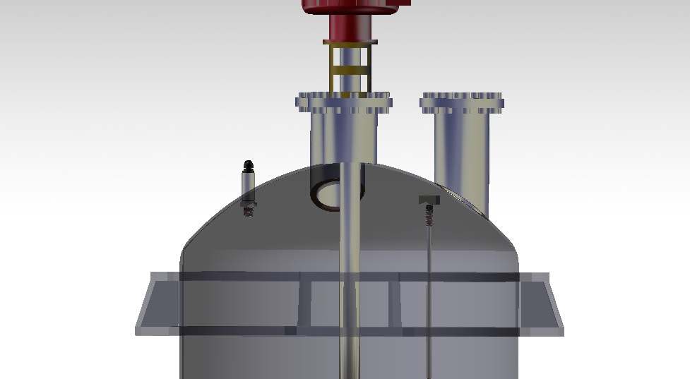
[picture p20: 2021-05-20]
Engenharias/Eletrônica/Integração/Integração - estrutura/Prints da Integração/Reator 2.jpg

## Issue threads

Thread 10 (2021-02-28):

Ajustes do Relatório do Ponto de Controle 1

Mateusas3s, 2021-02-28:
Escrever sobre o contexto do projeto:

- [x] apontando o cenário mundial do CO2, a busca por resolver esse problema, os elementos que impulsionam a busca por resolver esse problema como iniciativas de incentivo dos governos, investimento, legislação e também citar algumas soluções em uso em pesquisa
- [x] escrever um pouco sobre a captura direta de CO2 do Ar, introduzindo simplificadamente o que é a tecnologia, suas etapas, os tipos de modelos e suas características, fazer uma comparação com outras formas de atacar o problema do co2 e apontar trabalho e produtos relacionados ao DAC.

- [x] Reestruturar Introdução e TAP
- [x] Objetivo Geral
- [x] Definir Qtd. de CO2 capturado e qtd. de Carbonato de Cálcio gerado
- [x] Objetivos Específicos
- [x] EAP
- [x] Atualizar cronograma
- [x] Ajustar Metodologia (não é necessário explicar o método, mas como ele foi usado no projeto)
- [x] Escrever sobre a produção de carbonato de cálcio preciptado
- [x] Dar mais fuidez na escrita do relatório conectando os pontos
- [x] Ajustar fluxo de Trabalho
   - [x] Dinâmica de escrita e revisão do relatório
   - [x] Feedback Daily
- [x] Descrever melhor os Requisitos
- [x] Relacionar Atividades com o cumprimento de requisitos e o alcance dos objetivos
- [x] Refinar atividades definidas para se alcançar os objetivos
- [x] Um pouco mais sobre mercado de carbono
- [x] Formalização Técnica de figura, diagramas, escrita, cálculos

Mateusas3s, 2021-03-22:
A atividade de escrever o TAP foi unificada com a da Introdução a fim de serem melhor descritas e finalizar os pontos que faltaram.

Closed 2021-04-13.

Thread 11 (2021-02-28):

Descrever Metodologia de trabalho

Mateusas3s, 2021-02-28:
Descrever no relatório de PC:

- [x] A base metodologica usada no projeto
- [x] O Ciclo de vida do Projeto (etapas e fluxo de trabalho)
- [x] diagrama das etapas

Closed 2021-03-22.

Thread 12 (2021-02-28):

Plano de gerenciamento de Escopo

Mateusas3s, 2021-02-28:
Descrever no relatório do PC o seguinte:

- [x] Processo para levantamento e análise dos requisitos
- [x] EAP
- [x] descrever um pouco sobre backlog e o kanban

Closed 2021-03-22.

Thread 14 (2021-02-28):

Definir arquitetura do sub-sistema do Projeto

Mateusas3s, 2021-02-28:
Definir arquitetura do projeto e apresentar seus diagramas, fluxogramas, esquemáticos etc:
Cada área deve descrever a arquitetura planejada de seu subsistema num relatório na pasta do drive de sua respectiva área:

- [x] Visão Geral
- [x] Estrutura
- [x] Energia
- [x] Eletrônica
- [x] Software
- [x] Escrever no relatorio de PC

Baseanado-se na visão de arquitetura geral do sistema, cada área irá desenhar a arquitetura de seu respectivo subsistema: https://jamboard.google.com/d/1_PWJ1QSv5nmeTvgGDwdeLmyWXFVFjpEbWFvMi7wom20/viewer?f=0

Mateusas3s, 2021-03-09:
Fluxograma geral do sistema : https://jamboard.google.com/d/1_PWJ1QSv5nmeTvgGDwdeLmyWXFVFjpEbWFvMi7wom20/viewer?f=0

Baseando-se nele desenhar a arquitetura das dos demais subsistemas

Closed 2021-04-13.

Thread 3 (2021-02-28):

Elaborar EAP

Mateusas3s, 2021-02-28:
Desenhar EAP das etapas e ativiadades a serem realizadas no projeto.

- [x] Desenhar EAP
- [x] Escrever no relatório

Aguns exemplos que se encontram na pasta do drive "PI2-exemplo" podem ajudar.
EX:
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

Closed 2021-04-06.

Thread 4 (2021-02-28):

Levantamento dos requisitos do projeto

Mateusas3s, 2021-02-28:
Listar requisitos do projeto por área:
Cada área deve listar os requisitos de seu subsistema num relatório na pasta do drive de sua respectiva área:

- [ ] Geral
- [x] Estrutura
- [x] Energia
- [x] Eletrônica
- [x] Software
- [ ] escrever no relatório de PC
- [ ] Mapear interseção áreas dos requisistos

Planilha dos Requisistos: https://docs.google.com/spreadsheets/d/17YKsQn4F6uUskDw95l0J_6ED7kXgz-zIdlybI7A3s5M/edit?usp=sharing

Mateusas3s, 2021-03-08:
Reunião de quarta com Felício sobre IoT. (software + eletrônica) para fechar requisitos.

Mateusas3s, 2021-03-09:
adicionado link do esquema da visão geral da arquitetura do projeto

Closed 2021-03-22.

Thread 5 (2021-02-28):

Elaborar TAP

Mateusas3s, 2021-02-28:
Descrever o Termo de Abertura do Projeto contendo:

- [x] uma descrição do projeto
- [x] 5W2H
- [x] Tabela é /não é
- [x] Problemática do projeto(níveis de CO2 já na atmosfera, alto consumo energético no processo)
- [x] Justificativa (solução alternativa -> eliminar fases a partir do calcinador eliminando processos mais complexos e custosos; escopo da disciplina limitante; falar de possíveis clientes e a oportunidade de ser um produto real)
- [x] Objetivo (geral e específicos)

Closed 2021-03-22.

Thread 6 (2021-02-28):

PLano de gerenciamento do Tempo

Mateusas3s, 2021-02-28:
Descrever pontos de controle, prazos e marcos de entregas das atividades do projeto e adicionar ao PC:

- [x] Mapear atividades
- [x] Mapear datas de entregas, PC, reuniões
- [x] Elaborar cronograma Gatt

Closed 2021-03-22.

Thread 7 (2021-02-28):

Orçamento do Projeto

Mateusas3s, 2021-02-28:
Fazer orçamento inicial dos custos do projeto baseado nas escolhas Técnica de Componentes, Materiais e Tecnologias
Usar como base para colocar os preços encontrados na planilha do Drive: https://docs.google.com/spreadsheets/d/1k0OoqtMKl7v1P48zPOX0qNsBX_EcGFS0zaEiLMdEaSA/edit?usp=sharing
As planilhas de cada área estão separadas por abas num mesmo documento.

- [x] Mapear preço de componentes de cada sub-sistema
   - [x] Eletrônica
   - [x] Estrutura
   - [x] Energia
   - [x] Software
- [x] Justificativa das escolhas (Matriz de Decisão)
- [ ] Relacionar Componete com o requisito
- [ ] Mapear valor/hora de trabalho dos engenheiros
- [x]  adicionar no relatório de PC

Mateusas3s, 2021-03-22:
Tarefa cumprida parcialmente. Somente o time de eletrônica conseguiu trazer um orçamento preliminar dos componetes.

Closed 2021-05-19.

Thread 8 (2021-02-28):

Elaborar Plano de Comunicação

Mateusas3s, 2021-02-28:
Definir dinâmica de comunicação entre time do projeto, orientadores e partes interessadas:

- [x] definir ferramentas e objetivos
- [x] mapear partes interessadas
- [x] descrever no relatório de PC

Closed 2021-03-22.

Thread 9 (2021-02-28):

PLano de gerenciamento de Riscos

Mateusas3s, 2021-02-28:
Mapear riscos e formas de tratá-los :
Documento de referência para colocar os riscos está na Planilha no Drive : https://docs.google.com/spreadsheets/d/12hNz5elNELN_4asTPcDYu8esQTgaFbIIq79RtOt--9g/edit?usp=sharing

- [x] Mapear riscos do projeto
- [x] Identificar causas e efeitos dos riscos
- [x] Definir formas de previnir e corrigir problemas
- [x] Mapear áreas de interseção dos riscos
- [x] Análise SWot
- [x] adicionar no relatorio de PC

Closed 2021-03-22.

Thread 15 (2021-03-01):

Pesquisa sobre IoT e Blockchain

Mateusas3s, 2021-03-01:
Buscar na literatura científica, trabalhos que envolvam as duas tecnologias integradas:

- [x] Salvar artigos e links no repositório do projeto
- [x] Fazer levantamento de pontos importatnes
- [ ] RSL IoT + Blockchain
- [ ] RSL IoT sistema interno + Blockchain sistema externo
- [ ] Validar se a ideia cabe no projeto

Mateusas3s, 2021-03-01:
Esse é o link do artigo que o Chaim mandou: https://www.mdpi.com/2079-9292/10/2/204/htm

Mateusas3s, 2021-03-09:
mudança nas diretrizes da atividade

Closed 2021-03-22.

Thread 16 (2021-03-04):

Definir primeira proposta do projeto

Mateusas3s, 2021-03-04:
Depois da orientação recebida na reunião do dia 03/003/21, optamos por definir a primeira versão do projeto usando como base a demanda de uma empresa que utilize Carbonato de Cálcio como insumo de seus produto. A partir dessa demanda definida, será possível determinar o quanto de CO2 deve ser extraido do ar e por sua vez dimensionar o tamanho do sistema e subsistemas.

Para isso será preciso:
- [x] Definir empresa e sua demanda mensal de Carbonato de cálcio
- [x] Fazer cálculo da quantidade de X de CO2 necessária para produzir Y de Carbonato de Cálcio
- [x] Dimencionar sistemas e subsistemas para atender os requisitos anteriores definidos

Closed 2021-03-22.

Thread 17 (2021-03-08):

PLano de gerenciamento de Qualidade

Mateusas3s, 2021-03-08:
1. Defina o Título da Issue
2. Descreva brevemente a Issue (podem ser adicionadas imagens)
3. Descreva as tarefas quesitos para finalizar a Issue
4. Classifique a Issue na opção Labels
5. Marque os responsáveis na opção Assignees

Descrever plano definido para monitoramento e controle da qualidade das ativiades realaizadas:

- [x] Definir papeis de validadores e inspetores
- [x] Definir dinâmica de validação e inspeção
- [x] Descrever no relatório de plano de controle

marcelostosjr, 2021-03-13:
comecei a desenvolver

Closed 2021-03-22.

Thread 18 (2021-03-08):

Mapear atividades

Mateusas3s, 2021-03-08:
Cada sub-área deve mapear as suas atividades ao longo do projeto em ordem cronológica:

- [x] Geral
- [x] Estrutura
- [x] Energia
- [x] Eletrônica
- [x] Software
- [ ] Relacionar Atividades com o alcance dos objetivos
- [x] Escrever no relatório de PC

Mateusas3s, 2021-03-22:
Atividades mapeadas precisam de um refinamento

Closed 2021-04-06.

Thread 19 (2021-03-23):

Planilha de Cálculos Estequiométricos

NadiaSales9, 2021-03-23:
- [x] Criar planilha que facilite a modificação dos parâmetros;

Link de refência para o cálculo:
- https://www.cell.com/joule/fulltext/S2542-4351(18)30225-3
- http://plataforma.seeg.eco.br/sectors/energia

Mateusas3s, 2021-03-23:
Lembrar de compartilhar o link da planilha quando já tiver uma versão primária

NadiaSales9, 2021-03-24:
Link da planilha: https://drive.google.com/file/d/1z8hyGxACh8x20TNibdbl5tbQbF2SE4LV/view?usp=sharing

Closed 2021-03-30.

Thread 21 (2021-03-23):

Estruturar melhor os Objetivos específicos do projeto

Mateusas3s, 2021-03-23:
A medida que avançarmos no projeto e isso ficar mais claro devemos estabelecer os objetivos específicos referentes a cada área do projeto:

- [ ] Geral
- [ ] Software
- [ ] Eletrônica
- [ ] Estrutura
- [ ] Energia
- [ ] Escrever no Relatório PC2

Pergunta as ser respondida por cada área: O que um determinado sub-sistema deverá atender para atingir o Objetivo Geral?

- Objetivo Geral:  criar um protótipo que viabilize um modelo comercial de sistema de captura direta de dióxido de carbono do ar, produzindo carbonato de cálcio de alta pureza.

Closed 2021-04-06.

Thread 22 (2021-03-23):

Dimensionamento do Ventilador

Mateusas3s, 2021-03-23:
Atividade:
- [x] Definir Quantidade de CO2 a ser capturado;
- [x] Mapear configuração de ventiladores diponíveis
- [x] Calcular Tempo de Reação do NaOH + CO2
- [ ] Dimensionar Filtro do Contator
- [x] Dimensionar Quantidade de ventiladores, em relação ao preço e gasto de energia

Closed 2021-04-13.

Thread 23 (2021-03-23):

Integração do sistema Iot e Blockchain

Mateusas3s, 2021-03-23:
Planejamento e elaboração do sistema integrado de IoT e Blockchain entre time de software e eletrônica,

Atividades:
- [x] Reunião Quarta (24/03)
- [x] Arquitetura de comunicação

Closed 2021-04-06.

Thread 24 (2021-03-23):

Coletar Feedback do time em relação ao PC1

Mateusas3s, 2021-03-23:
Objetivo é ter uma visão geral e de pontos específicos do time do projeto a fim de corrigir falhas e promover mudançar na organização:

- [x] Feedback gerência -> desenvolvedores
- [x] Feedback desenvolvedores -> gerência
- [x] Feedback gerência -> gerência
- [x] Feedback desenvolvedores -> desenvolvedores
- [x] Feedback Time -> Projeto em Geral
- [x] Elaborar Google Forms

Closed 2021-04-03.

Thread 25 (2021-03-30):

Destacar pontos relevantes do artigo (Niya et al., 2018)

Rdadamos, 2021-03-30:
Separar os pontos relevantes  do artigo _Design and implementation of an automated and decentralized pollution monitoring system with blockchains, smart contracts, and LoRaWAN_ (Niya et al., 2018, http://dx.doi.org/10.1109/NOMS.2018.8406329) que justifiquem os objetivos específicos e que possam ser usados como referência na documentação.

Closed 2021-04-13.

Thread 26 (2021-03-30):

Protótipo de alta fidelidade

Rdadamos, 2021-03-30:
Elaborar protótipo de alta fidelidade com as seguintes telas:
[x] cadastro
[x] login
[x] tela inicial (home)

roginaldosemog, 2021-04-12:
Feito!

[Visualizar protótipo](https://www.figma.com/file/EbJexfdEm0DIBTlOCYwa12/CATARCO?node-id=0%3A1).

Closed 2021-04-12.

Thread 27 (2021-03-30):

Planilha para monitoramento de gasto energético

Mateusas3s, 2021-03-30:
- [x] Pesquisar quanto de CO2 é emitido por quantidade de energia consumida.
- [ ] Definir porcentagem máxima de gasto de energia para o sistema
- [x] Construir planilha

Mateusas3s, 2021-04-06:
Dar uma olhada no artigo da Carbon para buscar um limite fundamentado

Closed 2021-04-13.

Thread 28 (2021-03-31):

Diagrama de Integração

Mateusas3s, 2021-03-31:
Fazer Diagrama que represente o projeto como um todo integrando todas as áreas.
Nele deve conter:
- Representação técnica de componentes
- Fluxos
- Ligação entre componentes
- Legenda

Closed 2021-05-19.

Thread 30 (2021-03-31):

Reunião para integração: eletrônica - estrutura

YasmineAndrade, 2021-03-31:
Pauta:
- mostrar componentes e atuadores em casa etapa do sistema
- pontuar dúvidas que temos sobre a estrutura
- ver demais coisas que precisam ser feitas para a integração

Closed 2021-04-17.

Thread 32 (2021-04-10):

Pendencias para o PC3

Mateusas3s, 2021-04-10:
- [x] Dimensionamento do Filtro/ sistema de realimentação
- [x] Tubulações e bombas
- [x] Disposição dos componentes
- [x] Sala de Operação
- [x] Central de Comando
- [x] Atuador do reservatório para saída de Ca(OH)2
- [ ] Mapeamento da perda de NaOH no sistema/ pureza do NaOH que sai da centrífuga e do CaCO3
- [ ] Cálculo estequiométrico para rastrear quantidade de CO2/ cálculo da perda por reação
- [ ] Tempo de Reação no Reator
- [x] Processo de Ligação do sistema
- [x] Valores ideais de funcionamento que devemos fixar/ fazer cálculo
- [ ] Ajustar valor máximo de gasto de energia do sistema

Closed 2021-05-19.
